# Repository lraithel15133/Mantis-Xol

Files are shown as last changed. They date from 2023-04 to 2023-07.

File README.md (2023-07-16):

# Mantis Xol 2 has been discontinued! Big update pushed which is much easier to assemble, maintain, and use. (https://github.com/Armchair-Engineering/Xol-Toolhead)

# Mantis Xol 2


## Description
Originally a project to slap 5020 blower fans onto Mantis, this toolhead variant started as an attempt to improve parts cooling, spurred on by Derpimus' noted cooling woes on his DOOMCube. After finding that the 5020s were just plain too fat to fit without looking like a standard Ender 3 Thingiverse special, I abandoned the large fan dream in favor of better cooling efficiency and lighter weight. This new and improved dream was also corrupted by my then budding and now all-consuming love for worm gears.

Join me on Discord (https://discord.gg/armchairengineeringsux)

## New Features for Xol 2
 - Cooler: Still a little ugly but better
 - Lighter: 260g-ish for Sherpa Mini
 - Rigid-er: I want to throw this thing across the room

#### Features:
 - Better airflow than Stealthburner (6-7 CFM through short ducts vs 4.6-5.2 CFM through long ducts)
 - Improved resonance management compared to Mantis 5015
 - Support for Sherpa Mini-pattern extruder mounting as well as Annex Engineering's **Double Folded Ascender** worm gear extruder
 - Support for JosAr's Klicky, VinnyCordeiro and WhoppingPochard's PCB Klicky, and Nionio6915's Euclid
 
#### Supported (incl. usermods/experimental):
|Hotends |Extruders |Probes |
|--- |--- |--- |
| Rapido HF | Sherpa Mini | VoronDesign's TAP |
| Dragon SF/HF | Orbiter 2 | Beacon (normal) |
| Revo Voron | Vz-hextrudort | (PCB) Klicky |
| Phaetus XG | DropEffect | Euclid |
| Bambulab | LGX Lite |--- |
| Dragon UHF Mini / NF Crazy |--- |--- |
 
#### Future Development (No ETA):
 - Bracing for PCB mounts
 - Quickdraw 2 support
 - Update DFA Bottom to latest version for slightly better heatset quality of life
 - Port nozzle LEDs to Xol 2 (see usermods)
 - Port MMU sensor support to Xol 2
 - Confirm fitment for MattTheBaker's Beacon

## Build Notes:
This toolhead might require other modifications to retain full functionality of your printer. 
 - All test machines used for this mod had Rama's front idlers which have a much lower profile compared to stock Voron front idlers. The fan assemblies might conflict and reduce usable X travel.
 - The Klicky Probe carriage that was adapted was originally designed for the Dragon hotend. You'll need to use a taller probe body to reach the bed such as the one used by [Unklicky BFP](https://github.com/majarspeed/Unklicky). *This isn't an issue for Euclid or PCB Klicky*.
## Bill of Materials 
|Item|Count|Note|
|----|-|--|
|Rapido or XG|1|
|4010 24v blower fans|2|Add Polulu 3796 if you want the fancy 12v Deltas|
|2510 24v axial fan|1|
|M2x8 SHCS|2|
|M2x12 SHCS|4|
|M2x20 SHCS|2|
|M2.5x20 SHCS|4|
|m3x6 BHCS|7|
|m3x8 BHCS|7|
|m3x20 SHCS|2|
|M2 Heatset 4L x 3.5 OD|11|
|M3 Heatset "Standard"|10|
|D2F-5L Microswitch|1|
|M2x8 or M2x10 Self-Tapping|1|Optionally 1 more M2 heatset and an M2x8 SHCS|
|6x3 magnets|3|
|ZIP TIES||
## Changelog
### 29 November 2022 - Beacon Support
- Release Day means Beacon Support. Find it in the Experimental folder.
### 27 November 2022 - Tap Support
- Release Day means Tap Support. Find it in the Experimental folder.
### 22 November 2022 -Revo Voron
- Added support for Revo Voron with the Sherpa Mini Hotend mount
### 10 November 2022 - Shiny shiny
- Added nozzle LED support. Find it in the Experimental folder.
### 23 October 2022
### 3 October 2022 - Xol 2
- Improved aesthetics
- Downsized HE fan to 2510
- No more self-tapping screws
- Added front brace for Sherpa Mini
- New ducts for Tridents with lead screws
- Miscellaneous printability improvements
### 3 Aug 2022 - Xol with Boots
- Added MGN9H carriages for PCB Klicky
- Added additional stabilization for ducts. Ideally, these are fastened with 2x M2x20 and M2 heatset inserts.


## Acknowledgement
[Long/Mandryd](https://github.com/mandryd/VoronUsers/tree/master/printer_mods/Long/Mantis_Dual_5015) for the Mantis toolhead.<br/>
[TheWarolf](https://github.com/TheWarolf/Voron-Personal-Mods/tree/main/V2/Long_Mantis_Toolhead) for the ERCF sensorized Hotend Mount.<br/>
[Derpimus](https://github.com/lraithel15133) for the exegesis, some CAD work, feedback, and just being a rad dude.<br/>
[KayosMaker](https://github.com/KayosMaker) for the MGN12 Klicky X-Carriage and CAN board mounts and spacers.<br/>
[JosAr](https://github.com/jlas1/Klicky-Probe) for Klicky.<br/>
[WhoppingPochard](https://github.com/tanaes) and [VinnyCordeiro](https://github.com/VinnyCordeiro/) for PCB Klicky.<br/>
[Nionio6915](https://github.com/nionio6915/Euclid_Probe) for Euclid. <br/>
[VoronDesign](https://github.com/VoronDesign) for this particular CoreXY flavor.<br/>
[AnnexEngineering](https://github.com/Annex-Engineering) for the Sherpa Mini and Double Folded Ascender extruders, and the K3 that influenced the air management of the ducts. And also for giving access to an early revision of the new DFA so it could be adapted for this toolhead.<br/>
[Clee](https://github.com/clee), you know what you did.  
[Takuya](https://github.com/T4KUUY4)... just added the 36mm SB2040 mount

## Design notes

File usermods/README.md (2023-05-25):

# Community Xol mods

---

|Creator |Mod title |Description |
|--- |--- |--- |
|Derpimus |Dragon Hotend |Adds Dragon SF/HF hotend support for Sherpa [TAP/No-TAP] |
|PrintStructor |BambuLabs Hotend |Adds BambuLabs hotend support for Sherpa [TAP/No-TAP]. Supports 2510 and 3010, also LEDs |
|T4KUUY4 |SB2040 36mm Mount |Adds mount to hold SB2040 board to sherpa |
|DW-Tas |SB Led Mod |Adds support to reuse your SB LEDs for a decretive LED logo on the hotend mount |
|DW-Tas |Xol 2 Hotend Mounts - Orbiter v2 |Adds support for Orbiter v2 extruder |
|DW-Tas |Xol 2 Hotend Mounts - VX-Hexdrudort-Low |Adds support for VZ Hextrudort and LGX lite extruders |
|iniqy | Dragon hotend | Adds Dragon SF/HF/UHF/Crazy hotend support for VZ Hextrudort + LGX Lite Extruders (print with a Sherpa carriage) [TAP/No-TAP] |
|KayosMaker| Klicky dock and mount | can be found in the MantisUsermods repo [here.](https://github.com/mandryd/MantisUsermods/tree/main/Usermods/KayosMaker/MGN12_Klicky/STLs) |
|KayosMaker| EBB36 and SHT36 Mounts for No-TAP Carriages | Mounts to carriage and can optionally tie in to Sherpa or VZHextrudort with a standoff. See repo linked below for printable standoffs. |
|KayosMaker| EBB36 and SHT36 Universal Mounts | Mounts to extruder motor screws via standoffs. Standoffs included that can be used for above mount, once gap is measured.  External repo [here.](https://github.com/KayosMaker/CANboard_Mounts) |

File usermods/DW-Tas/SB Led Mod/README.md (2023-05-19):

# LED mounts for Xol 2 using standard LED harness from Stealthburner

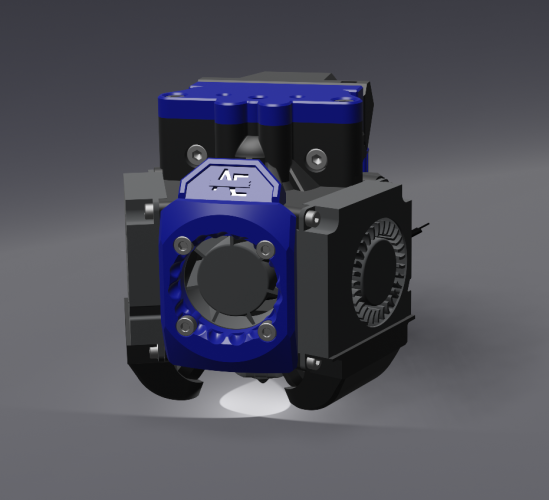
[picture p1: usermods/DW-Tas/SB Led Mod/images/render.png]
render


This mod uses the stock LED harness from Voron Stealthburner to add status and nozzle lights to Xol 2.

Depending on your build you will probably need a three wire extension between the Stealthburner LED harness and your toolhead board or standard wire harness.

There are now two versions to choose from. v1 is as per the render above. V2 is more compact and allows access to the bottom screw in the K-Plate if you use Sherpa Mini.

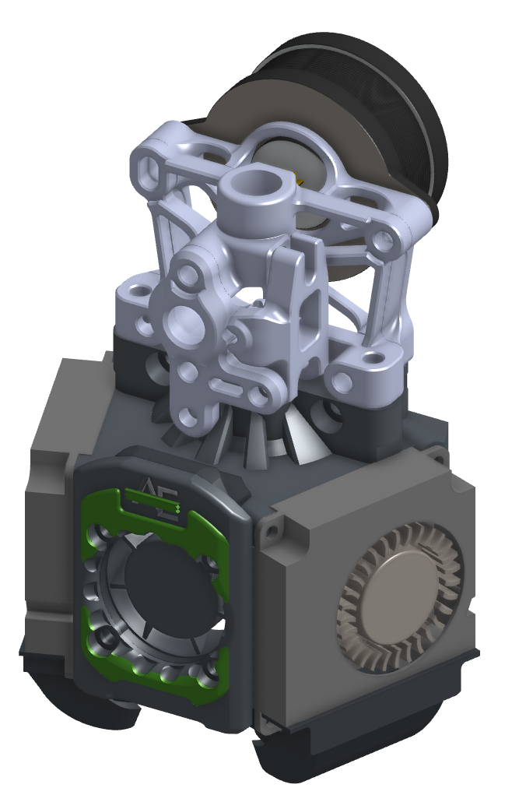
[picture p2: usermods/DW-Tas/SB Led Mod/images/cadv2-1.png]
v2 render


## What to print?
Print the ducts that suit your build. Standard or TAP availble for normal lenght or UHF length ducts are available

Print the faceplate parts for the version you want.
Both versions support neopixel and rainbow barf options.
Both versions require faceplate parts 1 & 2 and a diffuser to suit.
v1 requires an extra logo plate to be printed.

I recommend printing all of the faceplate parts, and diffuser parts in 0.1mm layer height 0.25 first layer will work fine.
Ducts can be printed the same as for standard Xol 2 ducts. Smaller layer heights may give you smoother walls on your ducts. I used 0.15mm layers.

## Assembly
This section is a work in progress.
for v2, standard neopixel versions, it works well to glue the white diffuser into the faceplate 1 part with a tiny drop of super glue.

## Wiring

Wires route under either side of the Xol 2 (behind a fan) and accross the 1st part of the faceplate where the status LED is inserted. Then behind the other fan before going down to the first duct. Then back accross to the other side under the 25mm hotend cooling fan behind the faceplate parts to the other duct. Look at the pictures below 😎

***Alternate wiring for non-UHF version.
You can put the 1st LED into the duct on the side all your wires go to first, then insert the 2nd LED into the "Status LED" location, and finally, the 3rd LED goes down to the other duct. If you insert the LEDs in this order, you will have to update your LED .cfg to make sure that the status LED is index #2 and that the others are index 1 and 3.

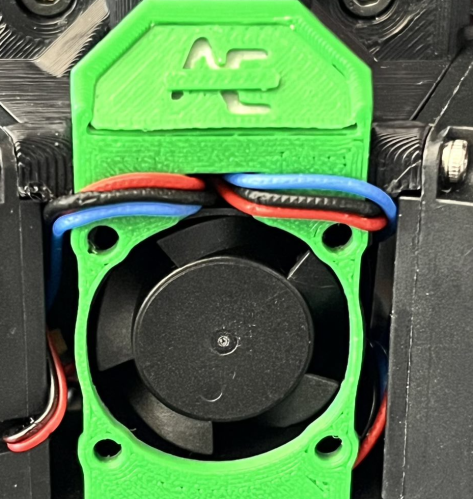
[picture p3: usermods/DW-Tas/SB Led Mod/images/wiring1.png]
wiring1


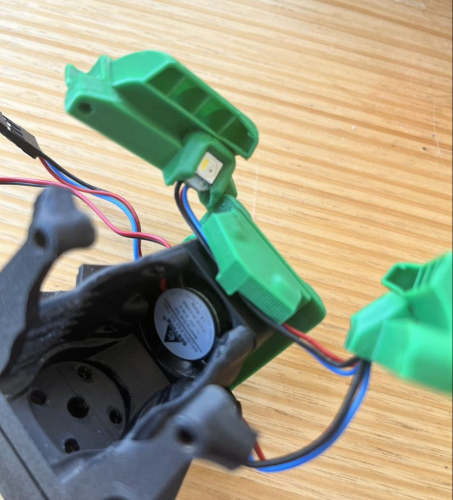
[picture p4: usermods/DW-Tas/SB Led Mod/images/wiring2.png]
wiring2


The cutout behind the updated front faceplate leaves space for the wires routed above the 25mm hotend cooling fan.

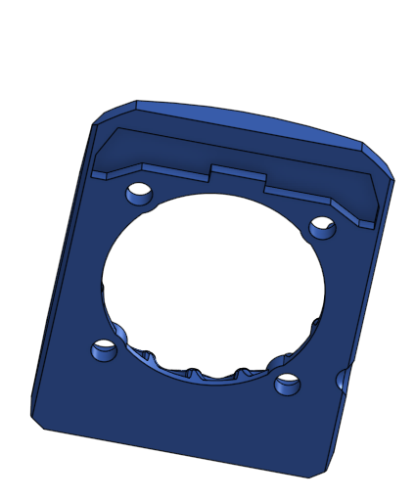
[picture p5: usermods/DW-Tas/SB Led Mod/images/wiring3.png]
wiring3


Only the front faceplate parts and ducts are changed from the standard hotend mounts and it uses the same m2 heatsets that would be used for stock Xol 2.

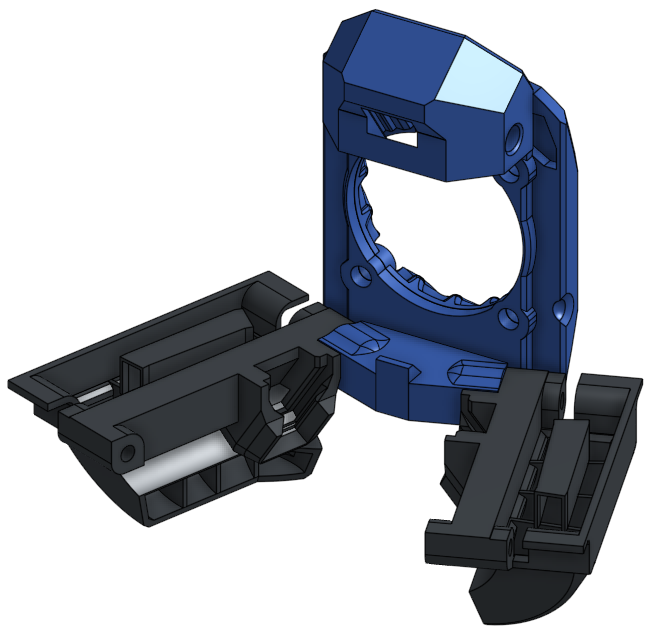
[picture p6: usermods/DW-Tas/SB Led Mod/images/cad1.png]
cad1


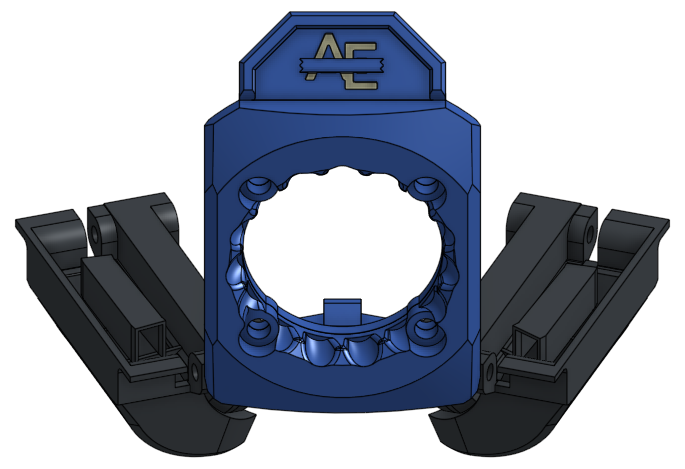
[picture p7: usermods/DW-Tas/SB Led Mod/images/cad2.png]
cad2


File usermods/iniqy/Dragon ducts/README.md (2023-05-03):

# Ducts

---

Use standard ducts for Dragon SF/HF with or without LED.

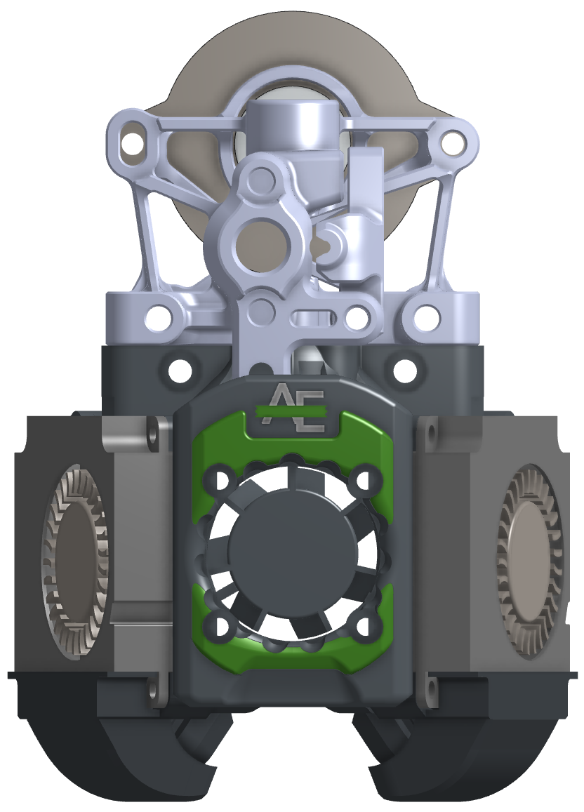
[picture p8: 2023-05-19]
usermods/DW-Tas/SB Led Mod/images/cadv2-2.png

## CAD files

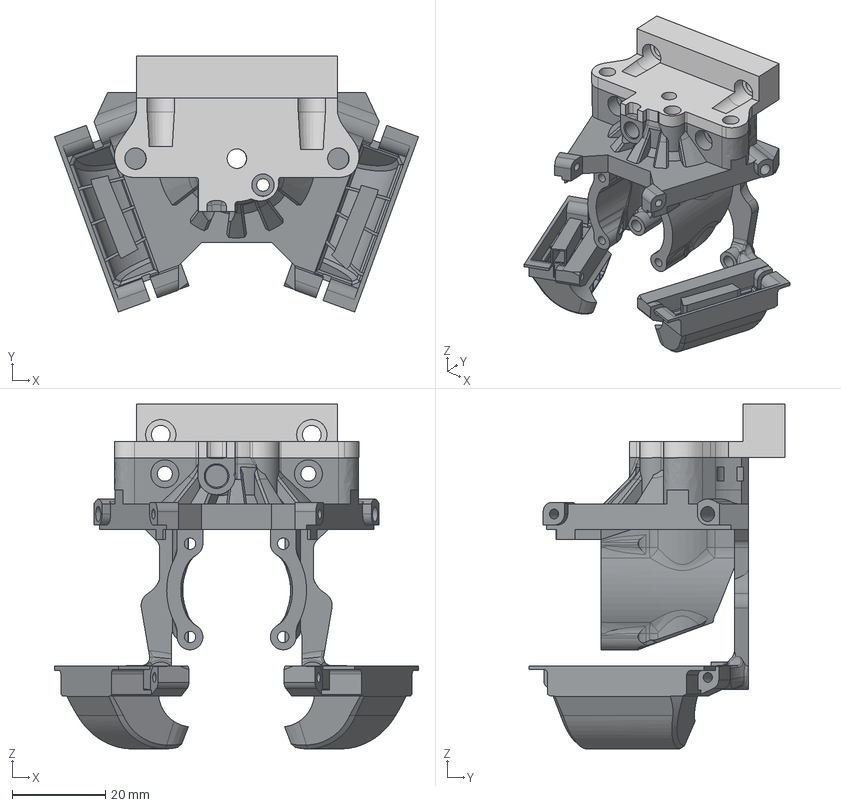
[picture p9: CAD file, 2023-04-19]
CAD/Xol 2/TAP/XolTapRapido.step
78.1 x 54.9 x 73.9 mm

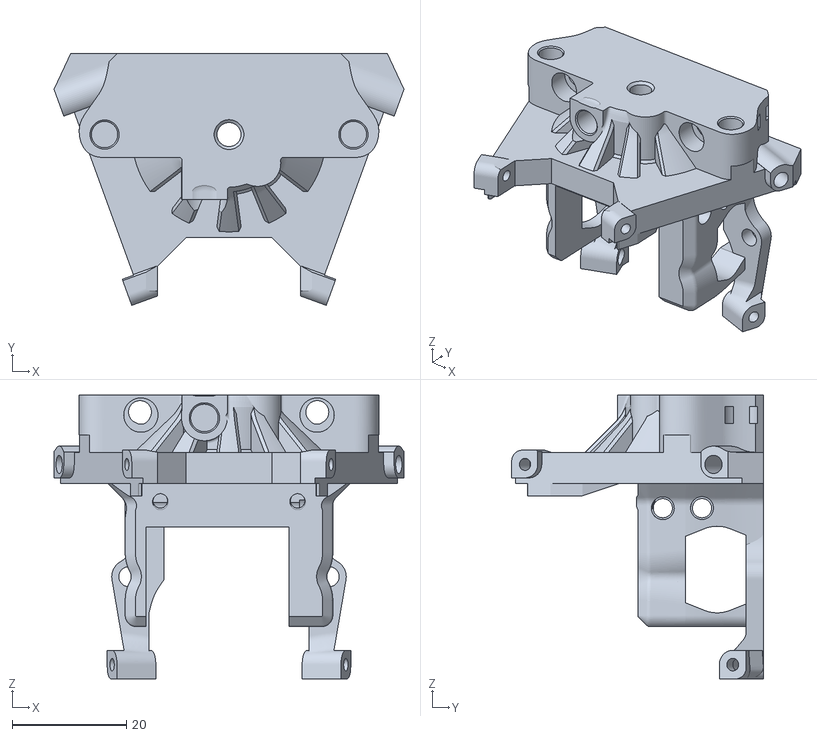
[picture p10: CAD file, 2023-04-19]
STL/Xol 2/No-TAP/Bambu Lab/BambuLab Hotend Mount 30mm fan.stl
61.2 x 44.0 x 49.6

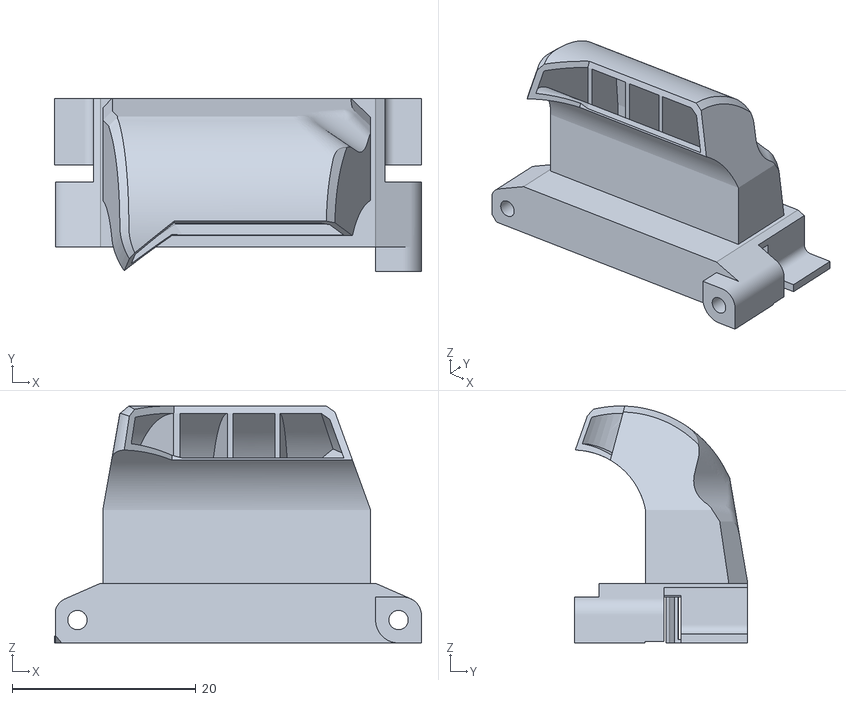
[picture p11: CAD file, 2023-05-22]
STL/Xol 2/No-TAP/Ducts/Xol 2 - Ducts UHF B - Tri-Vane Asym - Trident.stl
40.0 x 18.9 x 25.8

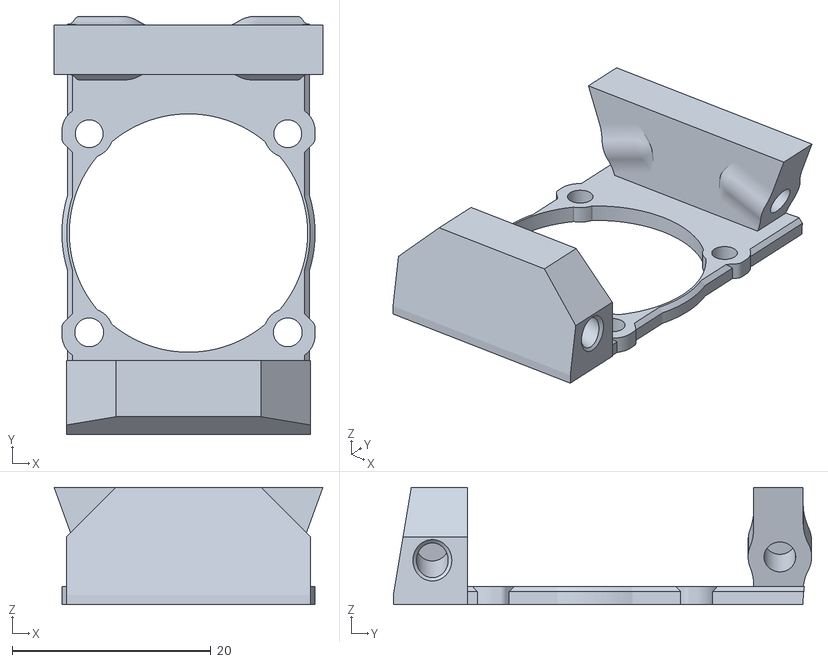
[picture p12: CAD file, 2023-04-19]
STL/Xol 2/No-TAP/Rapido/[a]_Xol 2 Rapido - Faceplate B.stl
27.1 x 42.1 x 11.8

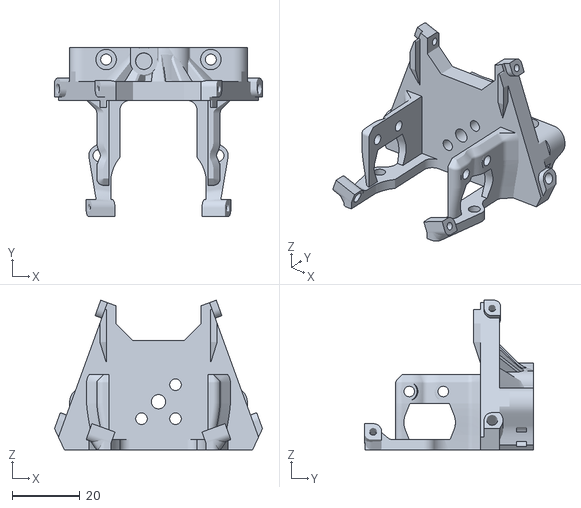
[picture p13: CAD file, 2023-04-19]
STL/Xol 2/No-TAP/XG/Xol 2 XG - Hotend Mount - Sherpa Mini.stl
61.2 x 49.6 x 44.0

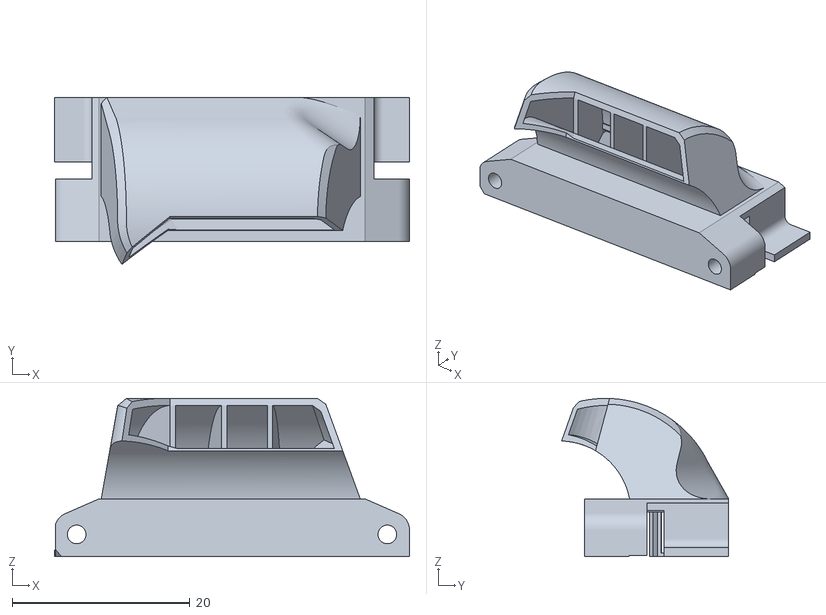
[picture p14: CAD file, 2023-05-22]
STL/Xol 2/TAP/Ducts/Xol 2 - Ducts - Tri-Vane Asym B - Trident - TAP.stl
40.0 x 18.8 x 17.8

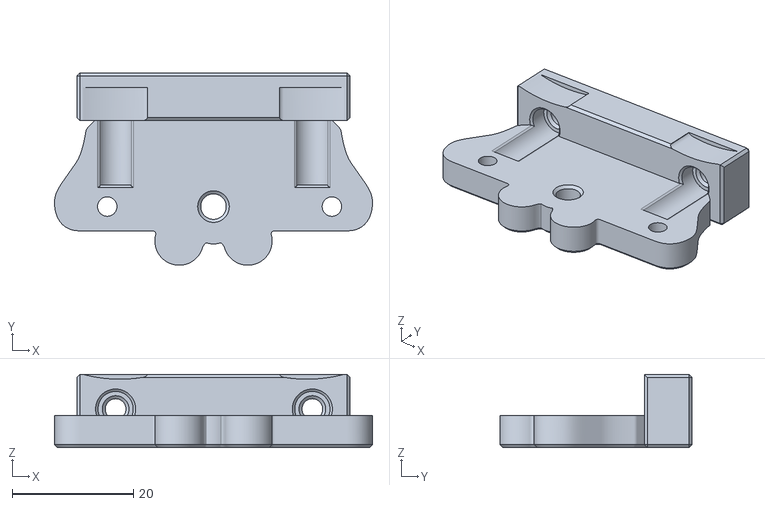
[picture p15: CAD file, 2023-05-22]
STL/Xol 2/TAP/Extruder/Xol 2 - Adaptor - Orbiter2 - TAP - RC8+.stl
52.4 x 31.7 x 12.1

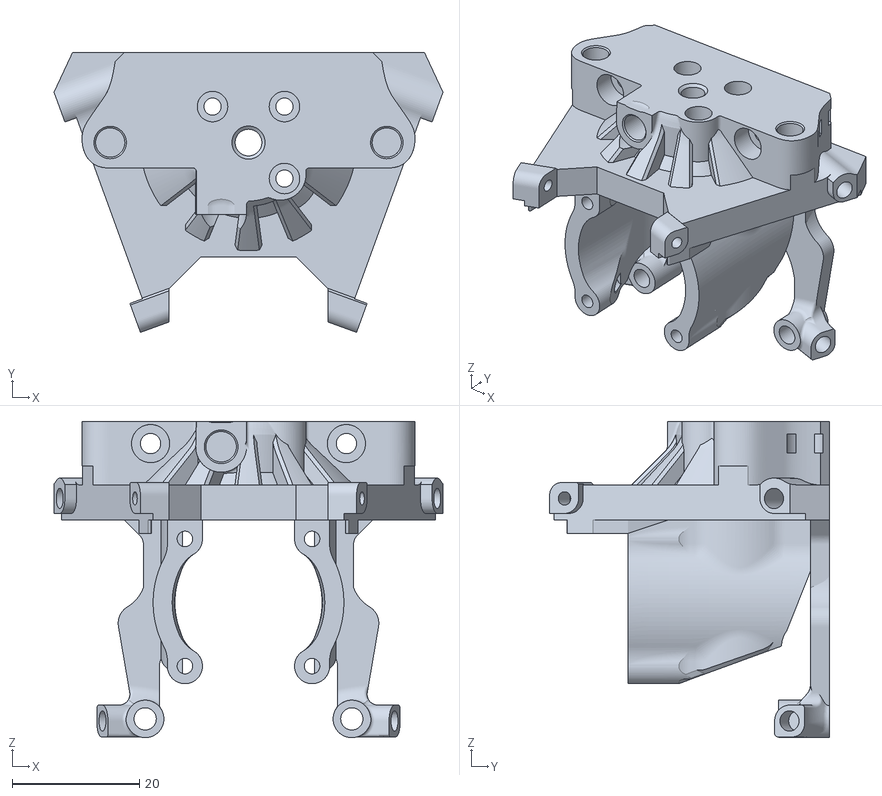
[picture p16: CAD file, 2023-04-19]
STL/Xol 2/TAP/Rapido/Xol 2 Rapido - Hotend Mount - Sherpa Mini - TAP.stl
61.2 x 44.0 x 49.7

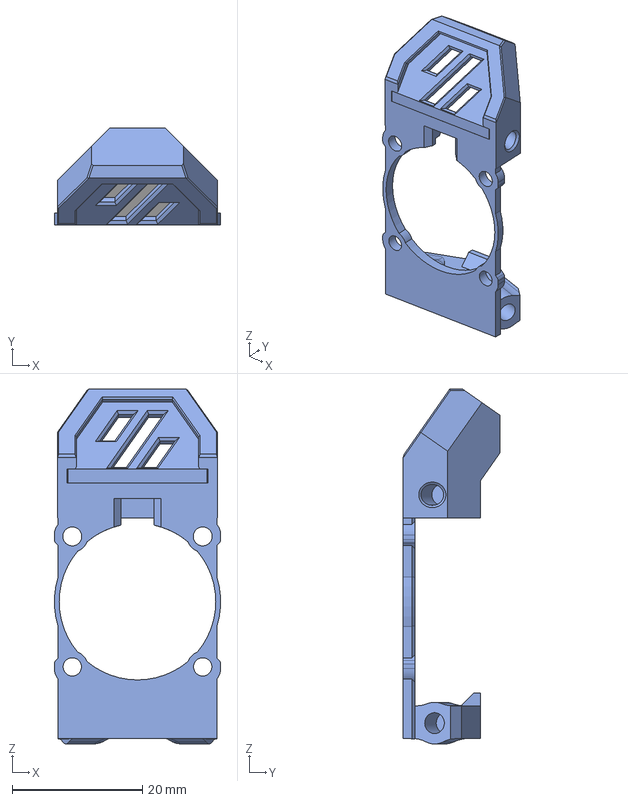
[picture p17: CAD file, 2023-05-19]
usermods/DW-Tas/SB Led Mod/CAD/Xol 2 - Stealthburner BARF.step
25.5 x 14.8 x 54.4 mm

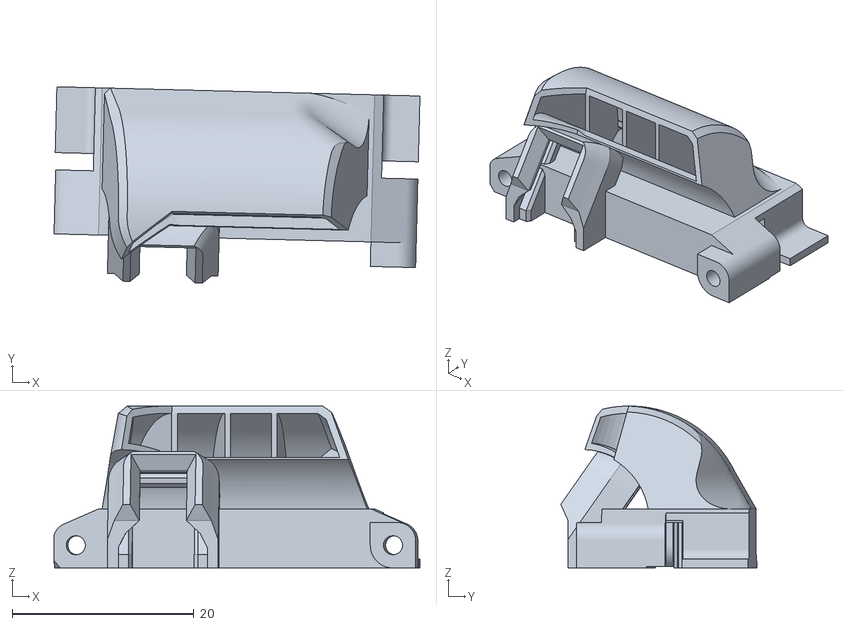
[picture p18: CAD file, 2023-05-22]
usermods/DW-Tas/SB Led Mod/STL/ducts/Xol 2 - LED - 4010 Ducts - Tri-Vane Right - Trident.stl
40.3 x 21.6 x 17.8

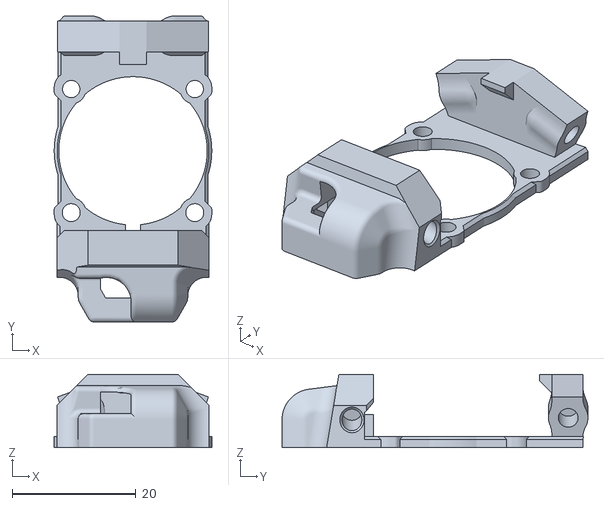
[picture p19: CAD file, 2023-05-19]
usermods/DW-Tas/SB Led Mod/STL/v2 faceplates/Faceplate - Rapido 1 - BARF v2 [needs support].stl
25.5 x 49.5 x 11.8

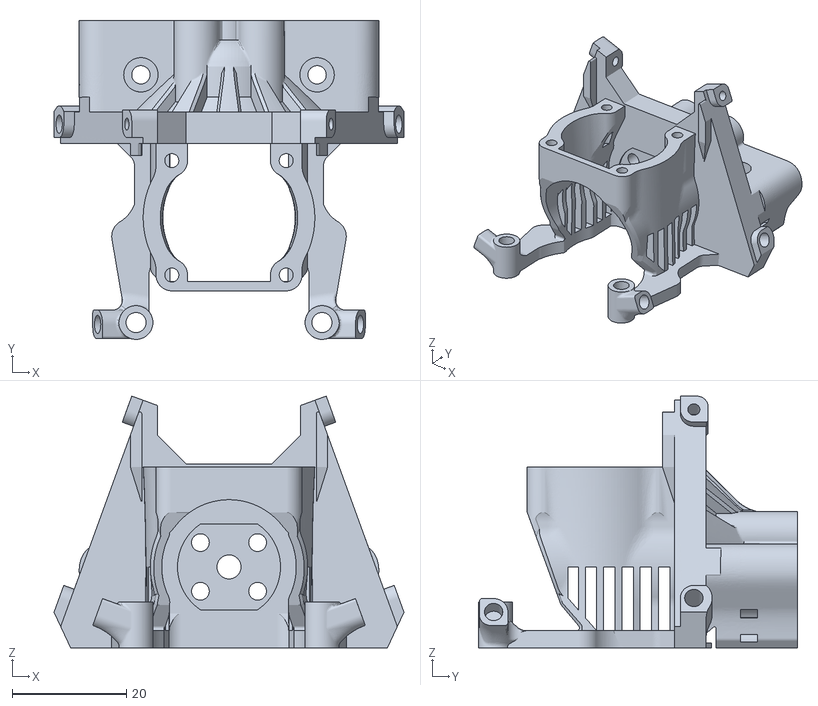
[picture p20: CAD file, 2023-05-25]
usermods/DW-Tas/Xol 2 Hotend Mounts - Orbiter v2/Xol 2 Revo Voron Orbiter2 - TAP.stl
61.2 x 55.7 x 44.0

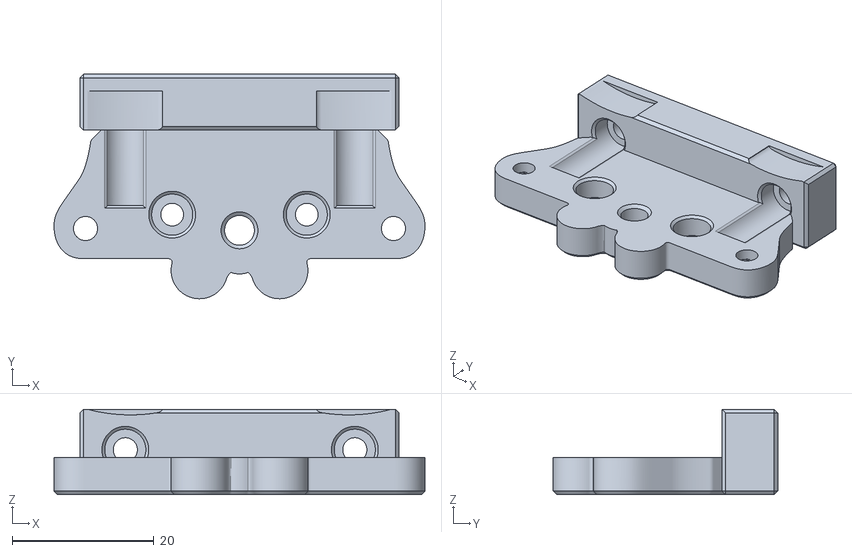
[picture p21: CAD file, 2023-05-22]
usermods/DW-Tas/Xol 2 Hotend Mounts - VX-Hexdrudort-Low/Xol 2 - Adaptor - VZ-Hextrudort-Low - TAP RC8+.stl
52.4 x 31.7 x 12.1

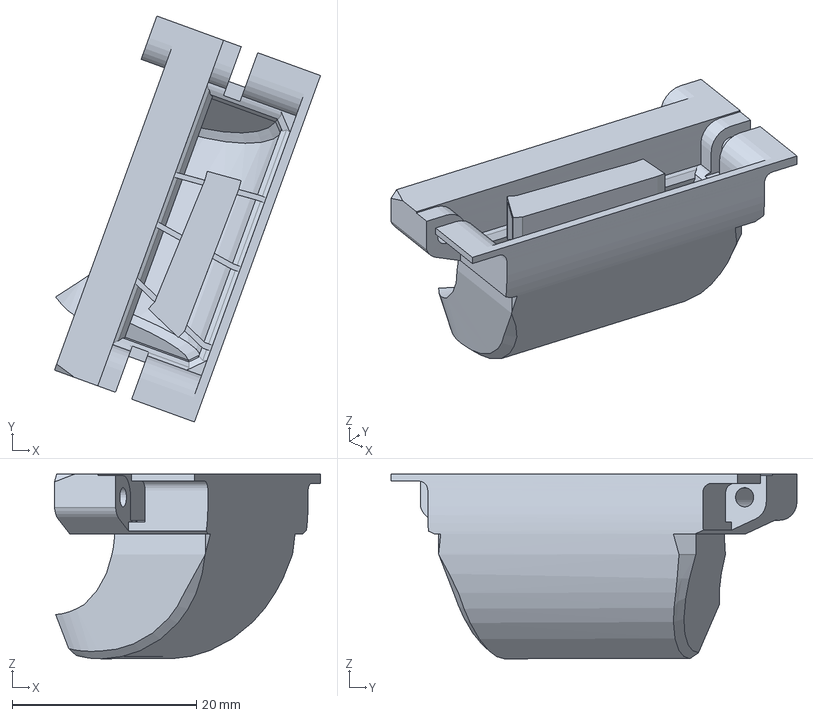
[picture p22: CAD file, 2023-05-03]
usermods/iniqy/Dragon ducts/Dragon UHF Mini & Crazy/Duct - Short Tri-Vane 2.3mf
28.9 x 44.1 x 20.0 mm

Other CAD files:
STL/Xol 2/TAP/Phaetus XG/Xol 2 XG - Hotend Mount - Sherpa - TAP.stl
STL/Xol 2/TAP/Revo Voron/Xol 2 Voron Revo - Hotend Mount - Sherpa - TAP.stl
usermods/iniqy/Dragon ducts/Dragon UHF/Mantis Xol - Ducts UHF - Tri-Vane Asym.stl
usermods/iniqy/Extruder/Xol 2 - Adapter - VZ-Hexdrudort-Low.3mf
STL/Xol 2/No-TAP/Bambu Lab/BambuLab Hotend Mount 25mm fan.stl
STL/Xol 2/No-TAP/Bambu Lab/Faceplate BambuLab 30mm fan w LED.stl
STL/Xol 2/No-TAP/Bambu Lab/Xol 2 - LED Holder.stl
STL/Xol 2/No-TAP/Bambu Lab/Xol 2 ADXL Mount.stl
STL/Xol 2/No-TAP/Ducts/Xol 2 - Duct UHF A - Tri-Vane.stl
STL/Xol 2/No-TAP/Ducts/Xol 2 - Duct UHF B - Tri-Vane.stl
STL/Xol 2/No-TAP/Ducts/Xol 2 - Ducts - Tri-Vane Asym A.stl
STL/Xol 2/No-TAP/Ducts/Xol 2 - Ducts - Tri-Vane Asym B - Trident.stl
STL/Xol 2/No-TAP/Ducts/Xol 2 - Ducts - Tri-Vane Asym B.stl
STL/Xol 2/No-TAP/XG/Xol 2 XG - Hotend Mount - DFA.stl
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

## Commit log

2023-04-19 Organized repo
    [BambuLab Hotend Mount 25mm fan.stl, BambuLab Hotend Mount 30mm fan.stl, Faceplate BambuLab 30mm fan w LED.stl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]
2023-04-23 SB LED reorg + voron logo plate
    [Faceplate - Rapido 1 - LED.stl, Faceplate - Rapido 2 - LED.stl, Logo plate [AE extra light cutouts].stl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]
2023-04-24 rename usermod folder to DW-TAS
    Have updated my github username and wanted to reflect it here.
    [Faceplate - Rapido 1 - LED.stl, Faceplate - Rapido 2 - LED.stl, Logo plate [AE extra light cutouts].stl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]
2023-04-24 added Dragon UHF Mini usermod
    [Duct - Tri-Vane 1 - Dragon UHF Mini.3mf, Duct - Tri-Vane 2 - Dragon UHF Mini.3mf, Xol 2 NF Crazy - Hotend Mount - VZ-Hexdrudort-Low v1.stl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]
2023-04-26 Added UHF ducts
    [Xol 2 - LED - 4010 Ducts - UHF - Tri-Vane - both - TAP.stl, Xol 2 - LED - 4010 Ducts - UHF - Tri-Vane - both.stl, Xol 2 - Stealthburner LED - UHF Ducts.step]
2023-05-01 Added buck holder mount CAD file
    [5v holder - Xol 2 Rapido - Hotend Mount - VZ - TAP - Xol 2 Rapido - Hotend Mount - VZ-Hexdrudort-Low - TAP + 5v stepdown holder.step]
2023-05-02 Added Crazy Dragon vz-hex non-tap
    [Xol 2 Crazy Dragon - VZ-Hextrudort-Low.step, Xol 2 Crazy Dragon - VZ-Hextrudort-Low.stl]
2023-05-02 added TAP mount
    [Duct - Short Tri-Vane 1.3mf, Duct - Short Tri-Vane 2.3mf, Duct - Tri-Vane 1 - Dragon UHF Mini.3mf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]
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2023-05-03 Fixed screw head room for VZ-Hex non-tap adapter and fixed STL orrientation
    [Xol 2 - Adapter - VZ-Hexdrudort-Low.stl, Xol 2 Bambu Lab 25mm fan - Hotend Mount - VZ-Hexdrudort-Low.stl, Xol 2 Bambu Lab 30mm fan - Hotend Mount - VZ-Hexdrudo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]
2023-05-03 Added crazy-dragon TAP vz-hextrudort version
    [Xol 2 Crazy Dragon - VZ-Hextrudort-Low - TAP.step, Xol 2 Crazy Dragon - VZ-Hextrudort-Low - TAP.stl]
2023-05-03 Update Xol 2 Crazy Dragon - VZ-Hextrudort-Low.step
    [Xol 2 Crazy Dragon - VZ-Hextrudort-Low.step]
2023-05-04 Added Dragon UFH version to VZ-Hextrudort-Low collection
    [Xol 2 Dragon UHF - VZ-Hextrudort-Low - TAP.step, Xol 2 Dragon UHF - VZ-Hextrudort-Low - TAP.stl]
2023-05-04 added non-tap dragon uhf vz-hex version
    [Xol 2 Dragon UHF - VZ-Hextrudort-Low.step, Xol 2 Dragon UHF - VZ-Hextrudort-Low.stl]
2023-05-04 Added Dragon S-HF VZ-Hex version
    [Xol 2 Dragon S-HF - VZ-Hextrudort-Low.step, Xol 2 Dragon S-HF - VZ-Hextrudort-Low.stl]
2023-05-06 Updates to dragon version for VZ-Hextrudort
    [Xol 2 Crazy Dragon - VZ-Hextrudort-Low.step, Xol 2 Crazy Dragon - VZ-Hextrudort-Low.stl, Xol 2 Dragon UHF - VZ-Hextrudort-Low.step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]
2023-05-06 Removed SB LED mod from experimental STL folder
    [Xol 2 - LED - 4010 Ducts - Tri-Vane - Left - TAP.stl, Xol 2 - LED - 4010 Ducts - Tri-Vane - Left.stl, Xol 2 - LED - 4010 Ducts - Tri-Vane - Right - TAP.stl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]
2023-05-11 Added BARF version to SB LED mod
    [Faceplate - Rapido 1 - BARF.stl, Faceplate - Rapido 2 - LED.stl, Voron Logo - BARF.stl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]
2023-05-11 Moved CAD for barf to CAD folder
    [Xol 2 - Stealthburner BARF.step]
2023-05-12 Fed No-TAP UHF ducts some chocolate
    [Xol 2 - Duct UHF A - Tri-Vane.stl, Xol 2 - Duct UHF B - Tri-Vane.stl]
2023-05-13 QoL improvements for BARF LED mod
    [Faceplate - Rapido 1 - BARF.stl, Voron Logo - BARF.stl, Xol 2 - Stealthburner BARF.step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]
2023-05-16 LED v2 mod
    [Faceplate - Rapido 1 - LED v2.stl, Faceplate - Rapido 2 - LED v2.stl, [white] diffuser - LED v2.stl]
2023-05-16 Create Faceplate - Rapido 2 - LED v2 [voron].stl
    [Faceplate - Rapido 2 - LED v2 [voron].stl]
2023-05-16 Added v2 BARF LED mod
    [Faceplate - Rapido 1 - BARF v2 [needs support].stl, Faceplate - Rapido 2 - BARF v2.stl, [white]Diffuser - LED-BARF.stl]
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2023-05-17 More cable room under v2 LED mounts
    [Faceplate - Rapido 1 - BARF v2 [needs support].stl, Faceplate - Rapido 1 - LED v2.stl]
2023-05-17 updated LED v2 mod
    [Faceplate - Rapido 1 - LED v2.stl, Faceplate - Rapido 2 - LED v2 [DW Tas remix].stl, Faceplate - Rapido 2 - LED v2.stl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]
2023-05-18 v2 LED southern hemisphere edition
    [Faceplate - Rapido 2 - LED v2 [DW Tas remix].stl, Faceplate - Rapido 2 - LED v2 [Southern Hemisphere Edition].stl]
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2023-05-18 reorganise SB LED mod STLs
    [Faceplate - Rapido 1 - BARF v2 [needs support].stl, Faceplate - Rapido 1 - BARF.stl, Faceplate - Rapido 1 - LED v2.stl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]
2023-05-19 Delete Xol 2 - Duct UHF A - Tri-Vane .stl
    leftover file after reoriented files were added
    [Xol 2 - Duct UHF A - Tri-Vane .stl]
2023-05-19 Updated UHF LED Ducts
    [Xol 2 - LED - 4010 Ducts - UHF - Tri-Vane - both - TAP.stl, Xol 2 - LED - 4010 Ducts - UHF - Tri-Vane - both.stl]
2023-05-20 Create Xol 2 - Adaptor - VZ-Hextrudort-Low - TAP R8.stl
    [Xol 2 - Adaptor - VZ-Hextrudort-Low - TAP R8.stl]
2023-05-21 Trident Ducts standard and LED mod
    [Xol 2 - Ducts - Tri-Vane Asym B - Trident - TAP.stl, Xol 2 - Ducts UHF - Tri-Vane Asym B - Trident - TAP.stl, Xol 2 - Ducts UHF B - Tri-Vane Asym - Trident.stl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]
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2023-05-24 Added DW-Tas Orbiter v2 usermod folder
    [Xol 2 - Adapter - Orbiter2 - TAP RC6-.stl, Xol 2 - Adapter - Orbiter2 - TAP RC8+.stl, Xol 2 Bambu Lab 2510 Orbiter2 - TAP.stl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]
2023-05-25 add CAN bracket to usermods
    [SHT36_EBB36_bracket_for_XOL_no_tap.step, SHT36_EBB36_bracket_for_XOL_no_tap.stl, bracket_body_x1.stl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]
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
